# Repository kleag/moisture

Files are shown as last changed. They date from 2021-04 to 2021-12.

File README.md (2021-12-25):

A plant soil moisture management application using Arduino MKR 1000, moisture sensor and 5V pump.

This project contains the Arduino sketch in the [arduino folder](https://github.com/kleag/moisture/tree/main/arduino/moisture_lcd) and the [Django REST framework-based API](https://github.com/kleag/moisture/tree/main/). There is also example configuration files to deploy the application using nginx and gunicorn in [etc](https://github.com/kleag/moisture/tree/main/etc). It is up to you to learn how to deploy a Web service using Django, nginx and gunicorn but feel free to open issues if you have questions, suggestions or (constructive) critics on this project itself.

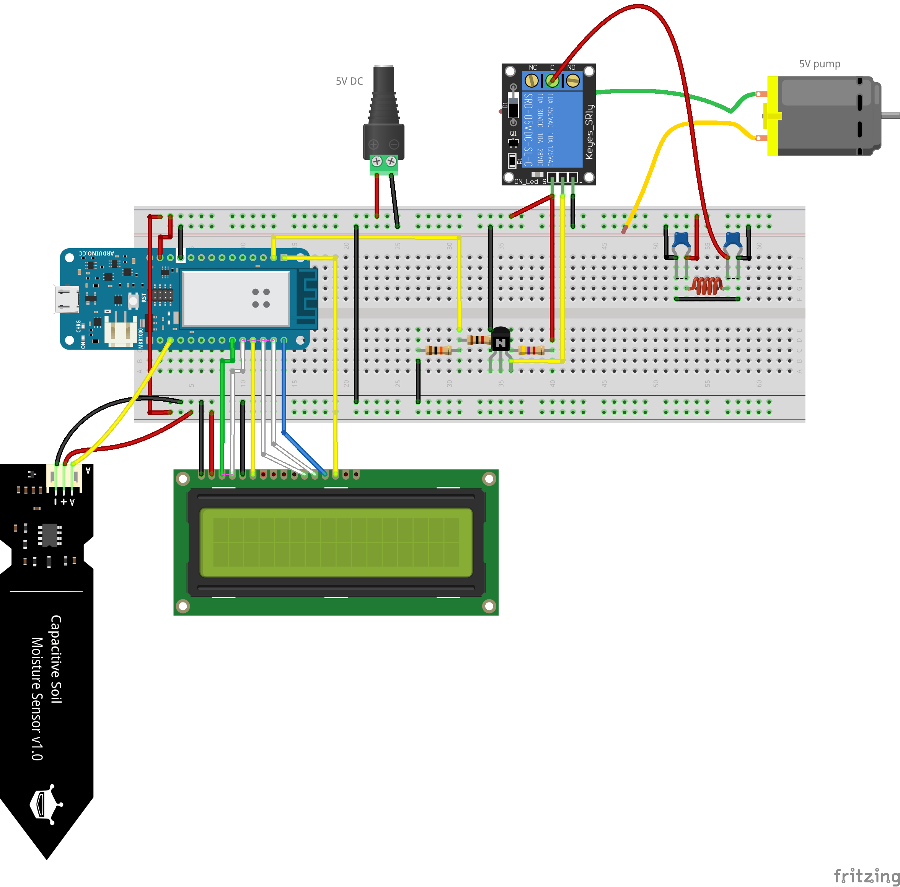
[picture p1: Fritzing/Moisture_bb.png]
Fritzing breadboard schema


This project was realized using [this kit available from Amazon](https://www.amazon.fr/gp/product/B0814HXWVV/ref=ppx_yo_dt_b_asin_title_o05_s00?ie=UTF8&psc=1). I had two problems using it. Firstly, the relay was open when HIGH on the Arduino pin and closed when LOW. Secondly, the pump was creating important electric perturbations, causing strange characters to appear on the screen and changes on the analog moisture measures.

Thanks to [this page](https://arduinodiy.wordpress.com/2018/08/07/re-inverting-an-inverting-relay/) and the [Electronique/Dépannage/Mécanique/Physique/Chimie/Informatique/Modélisme](https://www.facebook.com/groups/168734660482761/) Facebook group (thanks Olivia!), I was able to make it work as I wanted. You can see on the upper right the filtering part and on the lower right the transistor-based inverser.

After testing on the above breadboard, I made this perfboard schema:

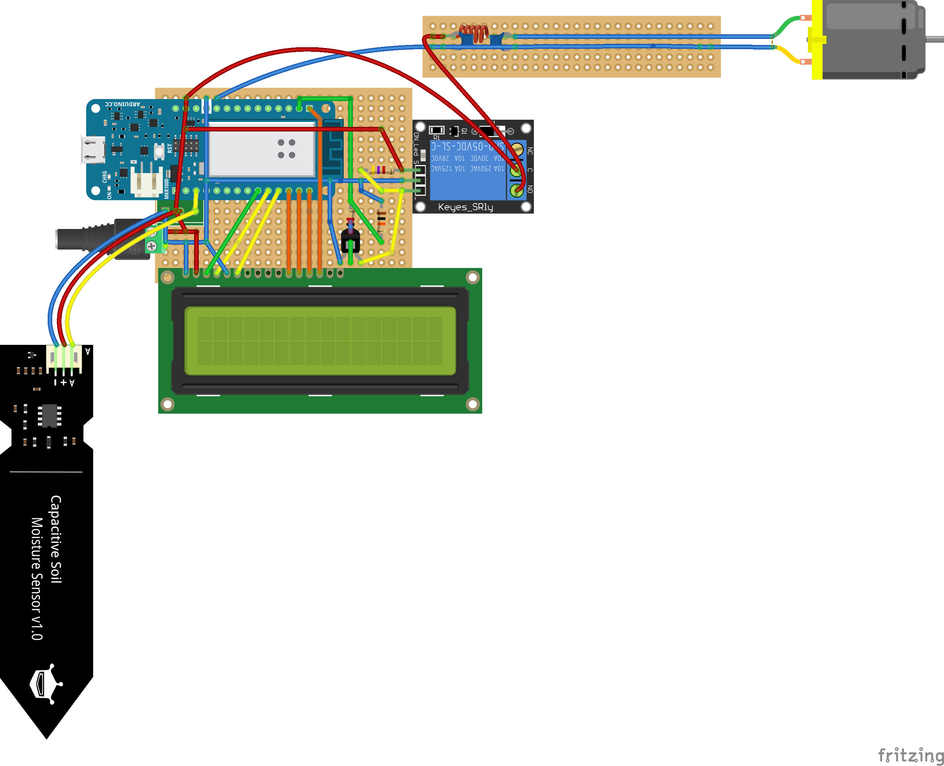
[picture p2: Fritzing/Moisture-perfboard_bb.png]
Fritzing perfboard schema


I made some little changes during the soldering itself and got this result:

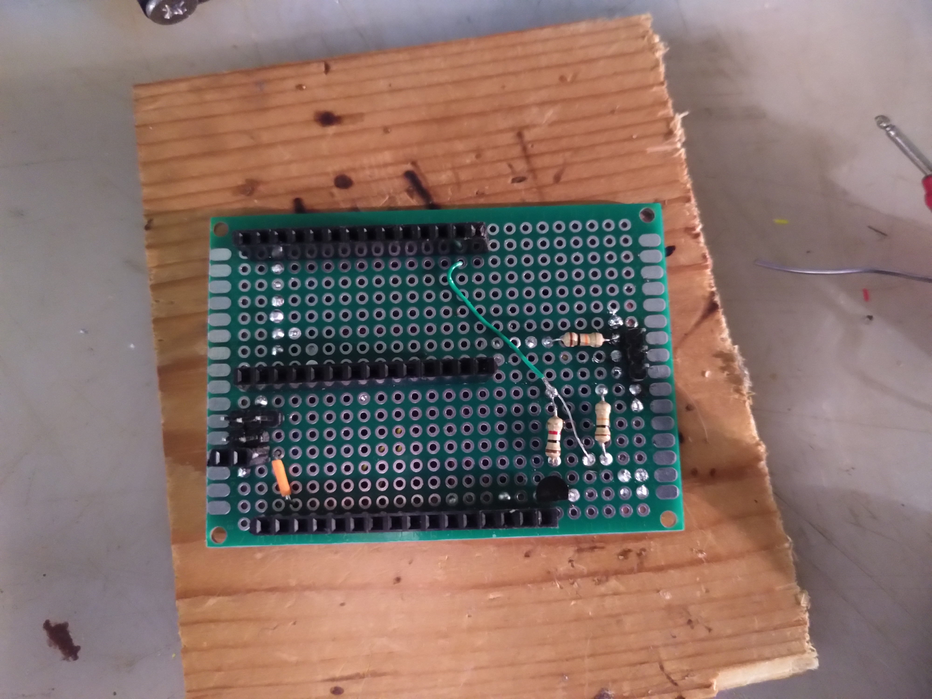
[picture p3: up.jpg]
Up of the soldered project
  - 
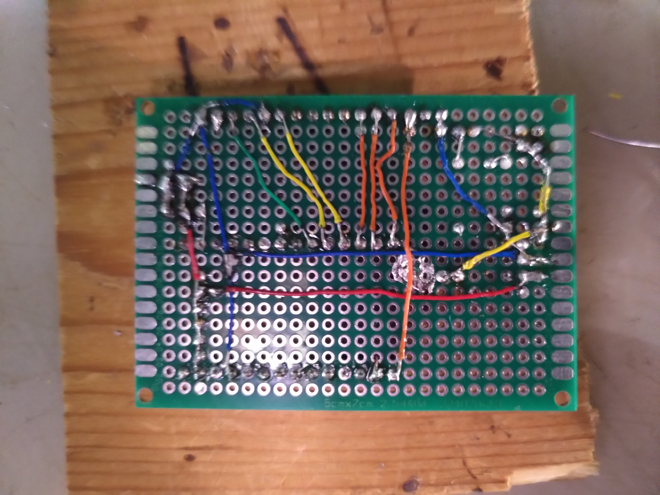
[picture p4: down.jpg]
Down of the soldered project
  - 

# Deployment

Starting the service in deploy mode:
```bash
$ sudo service gunicorn start
```

Starting the service in debug mode:
```bash
$ source /home/gael/miniconda3/bin/activate moisture
$ python manage.py runserver
```

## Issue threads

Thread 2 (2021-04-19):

Web service calls by the arduino takes too much time

kleag, 2021-04-19:
After sending a web service call from the arduino, the answer from the server takes way too much time to arrive. I don't know why.

kleag, 2021-05-01:
This is solved. But I don't know exactly how.

Closed 2021-05-01.

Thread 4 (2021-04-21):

Forced to use a separate power for the pump

kleag, 2021-04-21:
Currently, when the pump is connected on the card to the same power as the arduino, the arduino fails at the end of the pumping dispite the filtering device. Having only one power, possibly a battery, would be a lot better.

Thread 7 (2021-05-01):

Should be able to send commands to the arduino

kleag, 2021-05-01:
This would allow to force
- a measure
- a pumping
- a reset

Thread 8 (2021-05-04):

Should add a physical button to manually initiate a pumping session

kleag, 2021-05-04:

kleag, 2021-05-07:
Added using
https://create.arduino.cc/projecthub/ronbentley1/button-switch-using-an-external-interrupt-7879df?f=1#comments

Must still update the schemas.

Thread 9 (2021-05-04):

Pumping events occur but the soil is still dry

kleag, 2021-05-04:
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

It seems that the pumping is not really made.

kleag, 2021-05-07:
The pump was not activated. After moving things around, it works again. I suppose it was a wrong contact on the circuit.

Closed 2021-05-07.

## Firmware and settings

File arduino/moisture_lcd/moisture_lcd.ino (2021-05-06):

#define __ASSERT_USE_STDERR

#include <assert.h>

#include <ArduinoHttpClient.h>
#include <WiFi101.h>
#include <LiquidCrystal.h>

// Put your secret data in this file (see SECRET_* below)
#include "arduino_secrets.h"

////////////////////////////////
// Web service parmeters

// Set where you moistureduino Web service is listening
const String serverAddress = "moisture.nsupdate.info";  // server address
const int port = 443;
//const String serverAddress = "192.168.1.21";  // server address
//const int port = 8000;

////////////////////////////////
// Hardware parmeters

// Pins used by your LCD screen
const int RS = 1, EN = 2, D4 = 3, D5 = 4, D6 = 5, D7 = 6;
// Other arduino pins used
const int RELAY_PIN = 7;
const int MOISTURE_PIN = A0;
// LCD screen contrast
const int CONTRAST_PIN = 0;
const int CONTRAST = 20;
const int MANUAL_PUMP_BUTTON_PIN = 8;

////////////////////////////////
// Software parameters

// MAX_DRY and MAX_WET: moisture sensor calibration. Check the measures given
// by your sensor whith completely wet and fully dry soils
const int MAX_WET = 506;
const int MAX_DRY = 867;
// Moisture percent under which pumping will be done
const int THRESHOLD = 15;
// Will send an alert if moisture does not raise after a pumping in the
// [ALERT_MIN, ALERT_MAX] interval in minutes
const int ALERT_MIN = 10;
const int ALERT_MAX = 30;
// Duratio of a pumping event in seconds
const int PUMPING_DURATION = 5;
// Delay in minutes between two measures and other actions in normal operation
const int LOOP_DELAY = 20*60*1000;
// Will wait at least PUMP_DELAY minutes between two pumpings
const int PUMP_DELAY = 60;


////////////////////////////////
// Secret parmeters

///////please enter your sensitive data in the Secret tab/arduino_secrets.h
/////// Wifi Settings ///////
const String ssid = SECRET_SSID;    // your network SSID (name)
const String pass = SECRET_PASS;    // your network password (use for WPA, or use as key for WEP)
const String login = SECRET_LOGIN;        // your Web service user login
const String password = SECRET_PASSWORD;  // your Web service user password

WiFiSSLClient wifi;
//WiFiClient wifi;
HttpClient client = HttpClient(wifi, serverAddress, port);
const String contentType = "application/x-www-form-urlencoded";

/** Connect to the WiFi network */
void connectWifi() {
  int status = WL_IDLE_STATUS;
  while ( status != WL_CONNECTED) {
    Serial.print("Attempting to connect to Network named: ");
    Serial.println(ssid);                   // print the network name (SSID);

    // Connect to WPA/WPA2 network:
    status = WiFi.begin(ssid, pass);
  }

  // print the SSID of the network you're attached to:
  Serial.print("SSID: ");
  Serial.println(WiFi.SSID());

  // print your WiFi shield's IP address:
  IPAddress ip = WiFi.localIP();
  Serial.print("IP Address: ");
  Serial.println(ip);
  Serial.println("");
}

/** Post a message to an API endpoint of the Web service
 * @param url String. The path part of the url.
 * @param data String. The data to post.
 * @return int. The status returned by the Web service
 */
int post(const String& urlPath, const String& data) {
  Serial.print("making POST request: ");
  Serial.println(data);
  client.beginRequest();
  int post_result = client.post(urlPath);
  Serial.print("Post url set: ");
  Serial.println(post_result);
  client.sendHeader("Content-Type", contentType);
  client.sendHeader("Content-Length", data.length());
  Serial.println("Headers ready");
  client.sendBasicAuth(login, password); // send the username and password for authentication
  Serial.println("Basic auth sent");
  client.beginBody();
  client.print(data);
  Serial.println("Body written");
  client.endRequest();
  Serial.println("Request sent");


  // read the status code and body of the response
  int statusCode = client.responseStatusCode();
  Serial.print("Status code: ");
  Serial.println(statusCode);
//  String response = client.responseBody();
//  Serial.print("Response: ");
//  Serial.println(response);
  return statusCode;
}

/** Post a message to the /entries/ API endpoint of the Web service
 * @param raw int. The raw moisture level given by the sensor.
 * @param value int. Percent of moisture.
 * @return int. The status returned by the Web service
 */
int postEntry(int raw, int value) {
  char buffer[30];
  sprintf (buffer, "raw=%d&value=%d", raw, value);

  String postData = buffer;
  String urlPath = "/entries/";

  return post(urlPath, postData);
}

/** Post a message to the /entries/ API endpoint of the Web service
 * @param raw int. The raw moisture level given by the sensor.
 * @param value int. Percent of moisture.
 * @return int. The status returned by the Web service
 */
int postPumpingEntry(int duration) {
  char buffer[30];
  sprintf (buffer, "value=%d", duration);

  String postData = buffer;
  String urlPath = "/pumping_entries/";

  return post(urlPath, postData);

}

int postAlert() {
  String postData;
  String urlPath = "/alert/";

  return post(urlPath, postData);
}

/** handle diagnostic informations given by assertion and abort program
 * execution:
 */
void __assert(const char *__func, const char *__file, int __lineno, const char *__sexp) {
    Serial.println(__func);
    Serial.println(__file);
    Serial.println(__lineno, DEC);
    Serial.println(__sexp);
    Serial.flush();
    abort();
}

unsigned int loopDelay = LOOP_DELAY;

/// Last pumping time in milliseconds
unsigned long lastPumping = millis();
/// Last measured moisture percent
int lastPercent = 0;

/// The LCD display
LiquidCrystal lcd(RS, EN, D4, D5, D6, D7);

/**
 * Pump water during @ref duration, send the event to the Web service and
 * @return the time of this pumping event
 */
unsigned long pump(int duration) {
    assert(duration < 100);
    char buffer[30];
    sprintf (buffer, "Pumping %d second(s)", duration);
    Serial.println(buffer);

    digitalWrite(RELAY_PIN, HIGH);
    delay(duration*1000);
    digitalWrite(RELAY_PIN, LOW);
    delay(500);
    postPumpingEntry(duration);
    minutes_delay(1);
    measure();
    return millis();
}

/**
 * Measure the moisture level, write the result on the LCD screen and post the
 * result to the Web service
 * @result int, the measured moisture percent
 */
int measure() {
  int val = analogRead(MOISTURE_PIN);  // read the input pin
  int percent = constrain(map(val, MAX_DRY, MAX_WET,0, 100) , 0, 100);
  lcd.setCursor(0, 1);
  char buffer[10];
  sprintf (buffer, "%4d, %3d %%", val, percent);
//  sprintf (buffer, "%4d", val);

  Serial.println(buffer);
  lcd.print(buffer);
  postEntry(val, percent);
  return percent;
}

/**
 * Pause during @ref duration minutes
 * @param duration the number of minutes to wait
 */
void minutes_delay(int duration) {
  delay(1000*60*duration);
}

/**
 * Convert the @ref nb number of milliseconds to minutes
 * @param nb unsigned long, the number of milliseconds
 * @return unsigned long the number of minutes
 */
unsigned long millis2mn(unsigned long nb) {
  return nb/1000/60;
}

/**
 * Write an alert message on the LCD screen and post an alert entry to the Web
 * service
 */
void alert() {
  lcd.setCursor(0, 12);
  char buffer[10];
  sprintf (buffer, "ALERT");
  Serial.println(buffer);
  lcd.print(buffer);
  postAlert();
}

#define switched                            true // value if the button switch has been pressed
#define triggered                           true // controls interrupt handler
#define interrupt_trigger_type            RISING // interrupt triggered on a RISING input
#define debounce                              10 // time to wait in milli secs

volatile  bool interrupt_process_status = {
  !triggered                                     // start with no switch press pending, ie false (!triggered)
};
bool initialisation_complete =            false; // inhibit any interrupts until initialisation is complete

//
// ISR for handling interrupt triggers arising from associated button switch
//
void button_interrupt_handler()
{
  if (initialisation_complete == true)
  { //  all variables are initialised so we are okay to continue to process this interrupt
    if (interrupt_process_status == !triggered) {
      // new interrupt so okay start a new button read process -
      // now need to wait for button release plus debounce period to elapse
      // this will be done in the button_read function
      if (digitalRead(MANUAL_PUMP_BUTTON_PIN) == HIGH) {
        // button pressed, so we can start the read on/off + debounce cycle wich will
        // be completed by the button_read() function.
        interrupt_process_status = triggered;  // keep this ISR 'quiet' until button read fully completed
        loopDelay = 500; // we will loop quickly until switching and action are done
      }
    }
  }
} // end of button_interrupt_handler

bool read_button() {
  int button_reading;
  // static variables because we need to retain old values between function calls
  static bool     switching_pending = false;
  static long int elapse_timer;
  if (interrupt_process_status == triggered) {
    // interrupt has been raised on this button so now need to complete
    // the button read process, ie wait until it has been released
    // and debounce time elapsed
    button_reading = digitalRead(MANUAL_PUMP_BUTTON_PIN);
    if (button_reading == HIGH) {
      // switch is pressed, so start/restart wait for button relealse, plus end of debounce process
      switching_pending = true;
      elapse_timer = millis(); // start elapse timing for debounce checking
    }
    if (switching_pending && button_reading == LOW) {
      // switch was pressed, now released, so check if debounce time elapsed
      if (millis() - elapse_timer >= debounce) {
        // dounce time elapsed, so switch press cycle complete
        switching_pending = false;             // reset for next button press interrupt cycle
        interrupt_process_status = !triggered; // reopen ISR for business now button on/off/debounce cycle complete
        return switched;                       // advise that switch has been pressed
      }
    }
  }
  return !switched; // either no press request or debounce period not elapsed
} // end of read_button function

void manualPump() {
  Serial.println("manualPump");
  pump(5);
}

/**
 * Set up the pump relay, prepare the LCD screen and connect to WiFi
 */
void setup() {
  pinMode(MANUAL_PUMP_BUTTON_PIN, INPUT);
  attachInterrupt(digitalPinToInterrupt(MANUAL_PUMP_BUTTON_PIN),
                  button_interrupt_handler,
                  interrupt_trigger_type);

  pinMode(RELAY_PIN, OUTPUT);
  digitalWrite(RELAY_PIN, LOW);
  pinMode(CONTRAST_PIN, OUTPUT);
  analogWrite(CONTRAST_PIN, CONTRAST);
  Serial.begin(9600);
  // set up the LCD's number of columns and rows:
  lcd.begin(16, 2);
  // Print a message to the LCD.
  lcd.print("Moisture:");
  Serial.println("");
  connectWifi();

  // Wait some time to let the eventual first pumping to flow through the soil
  delay(2000);
  initialisation_complete = true; // open interrupt processing for business
}

void loop() {
  // test buton switch and process if pressed
  if (read_button() == switched) {
    Serial.println("Manual pump button has been pressed");
    // button on/off cycle now complete,
    manualPump();
    loopDelay = LOOP_DELAY; // switch back to default delay 
  }
  else {
    // measure moisture level and send result
    int percent = measure();
  
    unsigned long currentTime = millis();
    unsigned long elapsed = millis2mn(currentTime - lastPumping);
    char buffer[100];
    sprintf (buffer, "In loop. Elapsed: %d mn. Percent: %3d %%. Last percent: %3d %%.",
              elapsed, percent, lastPercent);
    Serial.println(buffer);
  
    // if, moisture level is too low, pump some water
    if (percent <= THRESHOLD && elapsed >= PUMP_DELAY)
    {
      lastPumping = pump(PUMPING_DURATION);
    }
    // check if moisture level has raised since the last pumping (if it occured
    // at least ALE RT_MIN mn ago (to let the water flow) and no more than
    // ALERT_MAX mn ago (such that it has not enough time to dry at all). If it
    // has not raised, write a message on LCD and send an alert message to the
    // Web service.
    else if (elapsed >= ALERT_MIN && elapsed <= ALERT_MAX
        && percent <= THRESHOLD && percent <= lastPercent) {
      alert();
    }
    lastPercent = percent;
  }
  delay(loopDelay);
}

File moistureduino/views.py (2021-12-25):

import logging
from django.core.mail import EmailMessage
from django.contrib.auth.models import User

import datetime
from django.utils import timezone
from rest_framework import mixins
from rest_framework import generics
from rest_framework import permissions
from rest_framework import renderers
from rest_framework import status
from rest_framework import viewsets
from rest_framework.decorators import action
from rest_framework.decorators import api_view
from rest_framework.response import Response
from rest_framework.reverse import reverse
from rest_framework.reverse import reverse_lazy

from plotly.offline import plot
from plotly.graph_objs import Scatter
from plotly.graph_objs import Bar
import plotly.graph_objs as go

from moistureduino.models import Alert
from moistureduino.models import Entry
from moistureduino.models import PumpingEntry
from moistureduino.serializers import AlertSerializer
from moistureduino.serializers import EntrySerializer
from moistureduino.serializers import PumpingEntrySerializer
from moistureduino.serializers import UserSerializer
from moistureduino.permissions import IsOwnerOrReadOnly

import moisture.settings as settings


# Get an instance of a logger
logger = logging.getLogger(__name__)


class AlertViewSet(viewsets.ModelViewSet):
    """
    This viewset automatically provides `list`, `create`, `retrieve`,
    `update` and `destroy` actions.

    Additionally we also provide extra `highlight`, `table`, `plot` and
    `reset` actions.
    """
    queryset = Alert.objects.all()
    serializer_class = AlertSerializer
    permission_classes = [permissions.IsAuthenticatedOrReadOnly,
                          IsOwnerOrReadOnly]

    @action(detail=False,
            permission_classes=[permissions.IsAuthenticated])
    def reset(self, request, *args, **kwargs):
        entries = Alert.objects.all()
        for entry in entries:
            entry.delete()
        api_root = reverse_lazy('api-root', request=request)
        return Response(status=status.HTTP_204_NO_CONTENT, data=api_root)

    @action(detail=True, renderer_classes=[renderers.StaticHTMLRenderer])
    def highlight(self, request, *args, **kwargs):
        alert = self.get_object()
        return Response(alert.highlighted)

    @action(detail=False, renderer_classes=[renderers.StaticHTMLRenderer])
    def table(self, request, *args, **kwargs):
        alerts = Alert.objects.all()
        rows = []
        for alert in alerts:
            cells = []
            cells.append(f"<td>{alert.created}</td>")
            cells.append(f"<td>{alert.message}</td>")
            scells = ''.join(cells)
            row = f"  <tr>{scells}</tr>"
            rows.append(row)
        srow = '\n'.join(rows)
        html = f"<html>\n<body>\n<table>\n{srow}\n</table>\n</body>\n</html>"
        return Response(html)

    def perform_create(self, serializer):
        serializer.save(owner=self.request.user)
        try:
            email = EmailMessage(
              'Moisture alert',
              ("This is an alert from your plant moisture management system. "
                "It is sent when the moisturing does not occur as expected. "
                "Please check your system."),
              settings.EMAIL_HOST_USER,
              [settings.EMAIL_HOST_USER],)
            logger.debug(f"Sending alert mail {settings.EMAIL_BACKEND}, "
                          f"{settings.EMAIL_HOST}, {settings.EMAIL_PORT}, "
                          f"{settings.EMAIL_USE_TLS}, "
                          f"{settings.EMAIL_HOST_USER}, XXXXX, "
                          f"{settings.DEFAULT_FROM_EMAIL}")
            email.send()
        except Exception as e:
            logger.error(f"Catch exception {e} in alert mail sending")

class EntryViewSet(viewsets.ModelViewSet):
    """
    This viewset automatically provides `list`, `create`, `retrieve`,
    `update` and `destroy` actions.

    Additionally we also provide extra `cleanup`, `highlight`, `table`, `plot` and
    `reset` actions.
    """
    queryset = Entry.objects.all()
    serializer_class = EntrySerializer
    permission_classes = [permissions.IsAuthenticatedOrReadOnly,
                          IsOwnerOrReadOnly]

    @action(detail=False,
            permission_classes=[permissions.IsAuthenticated])
    def reset(self, request, *args, **kwargs):
        entries = Entry.objects.all()
        for entry in entries:
            entry.delete()
        api_root = reverse_lazy('api-root', request=request)
        return Response(status=status.HTTP_204_NO_CONTENT, data=api_root)

    @action(detail=True, renderer_classes=[renderers.StaticHTMLRenderer])
    def highlight(self, request, *args, **kwargs):
        entry = self.get_object()
        return Response(entry.highlighted)

    @action(detail=False, renderer_classes=[renderers.StaticHTMLRenderer])
    def table(self, request, *args, **kwargs):
        entries = Entry.objects.all()
        rows = []
        for entry in entries:
            cells = []
            cells.append(f"<td>{entry.created}</td>")
            cells.append(f"<td>{entry.value}</td>")
            scells = ''.join(cells)
            row = f"  <tr>{scells}</tr>"
            rows.append(row)
        srow = '\n'.join(rows)
        html = f"<html>\n<body>\n<table>\n{srow}\n</table>\n</body>\n</html>"
        return Response(html)

    @action(detail=False, renderer_classes=[renderers.StaticHTMLRenderer])
    def cleanup(self, request, *args, **kwargs):
        entries = Entry.objects.all()
        nb_deleted = 0
        for entry in entries:
            if entry.raw == -1 and entry.value == "":
                entry.delete()
                nb_deleted += 1
        html = f"<html>\n<body>\n{nb_deleted} invalid entries have been removed\n</body>\n</html>"
        return Response(html)

    @action(detail=False, renderer_classes=[renderers.TemplateHTMLRenderer])
    def plot(self, request, *args, **kwargs):
        now = timezone.now()
        delta = datetime.timedelta(days=61)
        limit = now - delta

        logger.debug("try")
        x_labels = []
        x_data = []
        y_data = []
        xbar_data = []
        ybar_data = []
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

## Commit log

2021-04-12 Finished part 4 of Django REST framework tutorial
2021-04-13 Finish part 5 of Django REST framework tutorial
2021-04-13 Finished Django REST framework tutorial
2021-04-14 Add a reset action
    [serializers.py, views.py]
2021-04-14 Add arduino projects
2021-04-14 Add arduino secrets in gitignore
2021-04-14 Improve arduino code documentation
2021-04-14 Add alert posting to the arduino program
2021-04-15 Improve startup.
    Do a measure and a possible pumping during setup. Allows to speed up
    testing by detecting quickle too dry situations.
2021-04-16 Add fritzing schemas
    [Moisture-perfboard.fzz, Moisture-simple.fzz, Moisture.fzz]
2021-04-16 Remove pumping during setup
2021-04-20 Switch arduino sketch to https
2021-04-21 Switch back to http on local network
    My MKR1000 cannot access my Django REST framework API using https for an
    unknown reason.
    - question opened on Arduino forum: https://forum.arduino.cc/t/https-to-sites-using-letsencrypt-certificates-with-mkr1000/851421
    - issue opened on the Wifi101 github: https://github.com/arduino-libraries/WiFi101/issues/310
    [moisture_lcd.ino]
2021-04-21 Solve problem connecting to the https server
    The issue https://github.com/arduino-libraries/WiFi101/issues/310 was
    not in cause and will be closed. The problem was a nginx ssl config
    server side.
    [moisture_lcd.ino]
2021-04-21 Switch display text to English
    Switch to your own language if you wish.
2021-05-01 Update pumping events representation
2021-05-01 Update sensor calibration
2021-05-01 Split moisture and pumping into 2 different models
2021-05-01 Adapt arduino sketch to the new service API
2021-05-06 Add support for push button manual pumping
